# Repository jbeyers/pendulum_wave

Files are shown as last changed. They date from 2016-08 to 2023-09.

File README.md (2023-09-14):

# A perpetual pendulum wave machine

## What is it?

A pendulum wave is formed by a row of pendulums, each with a slightly different period. When started at the same time, they swing in a row, but quickly turn into a sinewavey snake shape, go through a whole set of interesting patterns and then end up in a straight row again.

The only ones I've seen are started and tuned manually.

## But perpetual?

Using steel bearing balls with magnets for the pendulums, and giving them a bit of a kick every now and again with a wire solenoid coil, the pendulums can be made to swing continuously. However, they would go out of tune after a few cycles.

The length of the pendulums are adjustable, so I can get them pretty close.

Getting the pendulums to vary their period is the tricky bit. This is slightly difficult to explain, but since the pendulums are built with fishing line, I can add a secondary pivot point below the first one, which will only kick in once the swing is larger than a certain angle. This causes the overall period to shorten if the angle increases.

Each coil has a sensing circuit to detect the pendulum swinging overhead. The coil is slightly offset to one side so that it can determine the direction of the swing from the slight difference in sensing time between the left and right swings.

Each coil is pulsed under PID control, so they sync up no matter what the initial positions are.

## License

This repository contains various files. In general, licensing is CC-BY-SA-4.0 for the designs and MIT for the software. Let me know if you need clarification.

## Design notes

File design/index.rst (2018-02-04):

Basic design
============

The design uses a frame made from square aluminium tubing, with 3D printed corner brackets I designed because I did not like any of the ones I found on Thingiverse. See `here<https://www.thingiverse.com/thing:2781519>`_ for the thingiverse design and the parts folder for the code.

Using a square box design is not the most stiff option, but it does allow me to resize the whole thing as I see fit.

The square tubing cut list spreadsheet has the list of cut lengths. I also designed brackets at the top to hang and adjust each pendulum to easily get the correct length for the period of the pendulum. The clips for the bearing balls are 3D printed and then drilled to ensure a smooth path for the line to go through. They simply clip onto the balls.

For the electromagnets, I got some 0.2mm wire from a friend. Doing 750 turns of wire around an air core should give me enough of an electromagnet to give the bearing balls a kick in the right direction. The coil will be slightly offset from each ball, to ensure that we can sense the direction.  

Sources:
--------

- Mantech: http://www.mantech.co.za/ProductInfo.aspx?Item=352M0029
- Banggood: https://www.banggood.com/0_2mm100m-Red-Copper-Magnet-Wire-Welding-Cable-Enameled-Wire-p-1081668.html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
- Aliexpress example: https://www.aliexpress.com/item/500-m-Free-shipping-0-19-mm-red-new-polyurethane-enameled-copper-wire-QA-1-130/2053713657.html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,searchweb201602_5_10152_10065_10151_10068_10344_10342_10343_10340_10341_10307_10060_10155_10154_10056_10055_10054_5370015_10059_10534_10533_10532_100031_10099_10338_10339_5580015_10103_10102_10052_10053_10142_10107_10050_10051_10174_10084_10083_10080_10082_10081_10110_5590015_10111_10112_10113_10114_143_10312_10314_10078_10079_10073-10051_10152_10111,searchweb201603_17,ppcSwitch_2&btsid=18ab4963-68ff-4cec-b533-50de82513f60&algo_expid=407fab98-5dce-4f39-aad7-5f68ff6fdf36-8&algo_pvid=407fab98-5dce-4f39-aad7-5f68ff6fdf36
- Ebay: http://www.ebay.com/itm/WINDING-WIRE-Copper-Enamelled-400g-Spool-0-10mm-3-00mm-/201975127992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

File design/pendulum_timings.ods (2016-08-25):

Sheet: Sheet1
Millisecond timings for 12 pendulums
Pendulum | 1 | 2 | 3 | 4 | 5 | 6 | 7 | 8 | 9 | 10 | 11 | 12
swings in 60 seconds | 64 | 63 | 62 | 61 | 60 | 59 | 58 | 57 | 56 | 55 | 54 | 53
period (ms) | 937.5 | 952.380952381 | 967.7419354839 | 983.6065573771 | 1000 | 1016.9491525424 | 1034.4827586207 | 1052.6315789474 | 1071.4285714286 | 1090.9090909091 | 1111.1111111111 | 1132.0754716981
integer ms period | 937 | 952 | 967 | 983 | 1000 | 1016 | 1034 | 1052 | 1071 | 1090 | 1111 | 1132
Last period error using integers | 32 | 24 | 46 | 37 | 0 | 56 | 28 | 36 | 24 | 50 | 6 | 4
Pendulum length (mm) | 218.3250114769 | 225.3109717837 | 232.637681324 | 240.3276664901 | 248.4053463915 | 256.897226949 | 265.8321186116 | 275.2413810433 | 285.1591986638 | 295.6228915734 | 306.67326715 | 318.3550185153
String length | 586.6500229539 | 600.6219435674 | 615.275362648 | 630.6553329801 | 646.8106927831 | 663.794453898 | 681.6642372233 | 700.4827620865 | 720.3183973275 | 741.2457831468 | 763.3465343001 | 786.7100370306
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

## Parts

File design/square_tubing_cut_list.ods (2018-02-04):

Pendulum wave box structure, lengths of 20mm aluminium square tubing needed
Box outside height | 395
Box outside depth | 200
Box outside width | 710
Square tubing width | 20
kerf width | 2
Item | Amount | Length (mm) | total
w side | 4 | 670 | 2680
depth side | 4 | 160 | 640
uprights | 4 | 355 | 1420
Top center spar | 2 | 670 | 1340
kerfs | 14 | 2 | 28
Total |  |  | 6108

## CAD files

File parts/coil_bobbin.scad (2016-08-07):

a = 25.8; // Overall length
b = 0.4; // flange thickness
c = 10.0; // flange diameter
d = 6.8; // ID of bobbin
e = 0.42; // Wall thickness

$fs=0.02;
translate ([0,0,a/2]) {
    // Center pillar
    difference() {
        union() {
            difference() {
                cylinder(a, r=c/2, center=true);
                cylinder(a-b*2, r=c/2, center=true);
                }
            cylinder(a, r=d/2 + e, center=true);
        }
        cylinder(a, r=d/2, center=true);
    }
}

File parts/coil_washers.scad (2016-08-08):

a = 0.8; // washer thickness
b = 3.2; // washer rim width
c = 6.4; // washer ID

$fs=0.02;
translate ([0,0,a/2]) {
    difference() {
        cylinder(a, r=(b+c)/2, center=true);
        cylinder(a, r=c/2, center=true);
    }
}

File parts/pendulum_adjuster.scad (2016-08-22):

a = 6; // Gap between bars
b = 20; // width of the bars
c = 29; // Width of whole thing
e = 3; // Outside wall thickness, and 45 degree area width
f = 160; // length of bar this must be in center of
g = 4; // Slot width for cable tie
h = 20; // Slide length
i = 4.5; // Screw hole diameter
j = 6.8; // Nut width
k = 0.5; // Slot for line
d = c-e-e; // Width of slot
m = 300; // Long distance for cutouts
n = 1; // Extra bit so cutouts go through without rendering
o = 1.6; // Thickness of cylinder springs for slider

t = 0.25; // tolerance

bar = [b+t+t, c, b+t];
l = e+t+b+t+f/2-(a/2+t+b+t+e);

$fs=0.02;

//pivot();
//translate([0, 35, 0]) adjuster();
//translate([0, 70, 0]) anchor();
translate([0, 105, 0]) slider();
//translate([0, 0, 0]) bar_support();


module pivot () {
    difference() {
        // Main block
        cube([e+t+b+t+a+t+b+t+e, c, b/2+e]);
        // Slots for bars to fit in
        translate([e, 0, e]) cube(bar);
        translate([e+t+b+t+a, 0, e]) cube(bar);
        // Cutout for free-hanging line
        translate([e+t+b+t, (c-d)/2, e]) cube([a, d, b]);
        // slot for line to go through
        translate([e+t+b+t, (c-d)/2, 0]) cube([a/2, d, b]);
        translate([e+t+b+t+a/2, (c-d)/2, e]) rotate([0,135,0]) cube([b, e, b+t+e]);
        translate([e+t+b+t+a/2, (c-d)/2+d-e, e]) rotate([0,135,0]) cube([b, e, b+t+e]);
        // Cable tie slot
        translate([0,(c-g)/2,-n]) cube([g/2, g, m]);
        // Slot to fit adjustment strip
        translate([e+t+b+t+a+t+b+t+e,c/2,0]) {
            translate([-e,-1.5*e-t,-n]) cube([e,t+3*e+t,m]);
            translate([-e-t-e-t,-2.5*e-t,-n]) cube([t+e+t,t+5*e+t,m]);
        }
    }
}


module adjuster () {
    difference() {
        // Main shape
        union() {
            cube([e,c,b/2+e]);
            translate([0,e,0]) cube([l, c-2*e, e]);
            // Slot to fit adjustment strip
            translate([l,c/2,0]) {
                translate([0,-1.5*e+t,0]) cube([t+e+t,3*e-2*t,e]);
                translate([t+e+t,-2.5*e+t,0]) cube([e-2*t,5*e-2*t,e]);
            }
        }
        translate([l,c/2-g/2,0]) cube([e, g, m]);
        // slot for cable tie
        translate([0,(c-g)/2,0]) cube([g/2, g, b+t+e]);
        // Slot for screw adjuster
        translate([e+t+b,c/2,0]) {
            translate([0,-c/4-t,0]) cube([t+e+t,t+c/2+t,e]);
            translate([t+e+t,-g/2,0]) cube([g,g,e]);
        }
    }
}


module anchor () {
    difference() {
        // Main shape
        hull() {
            translate([0,e+t,0]) cube([e,c-2*e-2*t,e]);
            translate([b+10,c/2,0]) cylinder(e, r=c/2-e-t);
        }
        // Slot and hole for cable tie
        translate([0,(c-g)/2,e-g/2]) cube([b+e,g,g]);
        translate([b+e,(c-g)/2,0]) cube([g/2,g,e]);

        translate([b+10,c/2,e]) cylinder(b,r=i/2,center=true);
        cube([b+e,c/4+t,e]);
        translate([0,3*c/4-t,0]) cube([b+e,c/4+t,e]);
    }
}

module slider() {
    difference() {
        // Main shape
        union() {
            translate([e,0,0]) cube([2*e,c,b]);
            translate([e,c/5,0]) cylinder(b,r=c/5,center=false);
            translate([e,4*c/5,0]) cylinder(b,r=c/5,center=false);
            translate([2*e,0,0]) cube([b,c,2*e]);
            // Slot to fit adjustment strip
        }
        // Hollow out the cylinders
        translate([e,c/5,0]) cylinder(b,r=c/5-o,center=false);
        translate([e,4*c/5,0]) cylinder(b,r=c/5-o,center=false);
        // slot for slider
        translate([e+0.4,e-2*t,0]) cube([t+e+t-0.4,c-2*e+4*t,b]);

        // Bolt and nut capture
        translate([3*e,(c-j)/2-t,e]) cube([b,j+2*t,2*e]);
        translate([e+10,c/2,e]) cylinder(b,r=i/2,center=true);
        // Line guides
        translate([e+10,0,e]) cylinder(b,r=i/2,center=true);
        translate([e+10,c,e]) cylinder(b,r=i/2,center=true);
        // Line capture slot
        translate([2*e+10+5,(c-k-t)/2,0]) cube([b,k+2*t,b]);
    }
}


module bar_support () {
    support_l = 2*b+4*t+a+2*e;
    difference() {
        // Main block
        cube([e+2*t+b+c,support_l, b/2+e]);
        // Bar cutouts
        translate([e,0,e]) cube([b+2*t,m,b]);
        translate([e,e,e]) cube([m,b+2*t,b]);
        translate([e,e+b+2*t+a,e]) cube([m,b+2*t,b]);
        translate([2*e+2*t+b,e+b+2*t+a/2,0]) {
            translate([0,-b/2-t,0]) cube([m,b+2*t,b]);
            translate([-g/2,-g/2,0]) cube([g,g,b]);
        }
        // Cable tie slots
        translate([-g/2,support_l/2-g/2,0]) cube([g,g,b]);
        translate([e+2*t+b+c/2-g/2,-g/2,0]) cube([g,g,b]);
        translate([e+2*t+b+c/2-g/2,support_l-g/2,0]) cube([g,g,b]);
    }
}

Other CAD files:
parts/pendulum_adjuster_anchor.scad
parts/corner_bracket.scad
parts/pendulum_adjuster_slide.scad
parts/pendulum_ball_holder.scad
parts/pendulum_pivot.scad

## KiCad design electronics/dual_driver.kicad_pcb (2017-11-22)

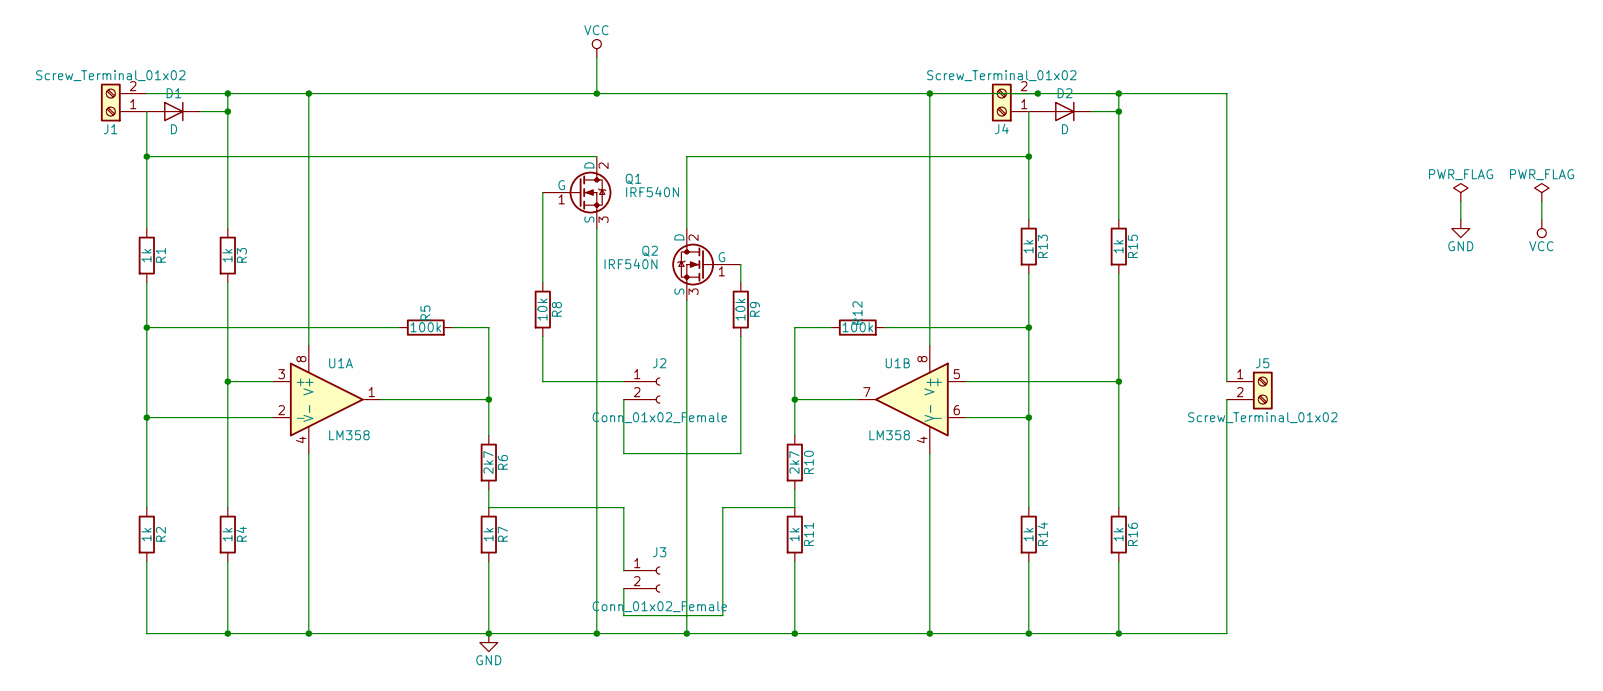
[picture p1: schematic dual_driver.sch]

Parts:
D1, D2: D; D_DO-41_SOD81_P2.54mm_Vertical_AnodeUp
J1, J4: Screw_Terminal_01x02; TerminalBlock_Phoenix_MPT-2.54mm_2pol
J2, J3: Conn_01x02_Female; Socket_Strip_Straight_1x02_Pitch2.54mm
J5: Screw_Terminal_01x02; TerminalBlock_bornier-2_P5.08mm
Q1, Q2: IRF540N; TO-220-3_Vertical
R1, R2, R3, R4, R7, R11, R13, R14, R15, R16: 1k; R_Axial_DIN0516_L15.5mm_D5.0mm_P20.32mm_Horizontal
R5, R12: 100k; R_Axial_DIN0516_L15.5mm_D5.0mm_P20.32mm_Horizontal
R6, R10: 2k7; R_Axial_DIN0516_L15.5mm_D5.0mm_P20.32mm_Horizontal
R8, R9: 10k; R_Axial_DIN0516_L15.5mm_D5.0mm_P20.32mm_Horizontal
U1: LM358; DIP-8_W7.62mm

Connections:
GND: J5.2, Q1.3 (S), Q2.3 (S), R2.2, R4.2, R7.2, R11.2, R14.2, R16.2, U1.4 (V-)
unnamed: D1.2 (A), J1.1, Q1.2 (D), R1.1
unnamed: D2.2 (A), J4.1
unnamed: J2.1, R8.2
unnamed: J2.2, R9.2
unnamed: J3.1, R6.2, R7.1
unnamed: J3.2, R10.2, R11.1
unnamed: Q1.1 (G), R8.1
unnamed: Q2.1 (G), R9.1
unnamed: Q2.2 (D), R13.1
unnamed: R1.2, R2.1, R5.1, U1.2 (-)
unnamed: R3.2, R4.1, U1.3 (+)
unnamed: R5.2, R6.1, U1.1
unnamed: R10.1, R12.1, U1.7
unnamed: R12.2, R13.2, R14.1, U1.6 (-)
unnamed: R15.2, R16.1, U1.5 (+)
VCC: D1.1 (K), D2.1 (K), J1.2, J4.2, J5.1, R3.1, R15.1, U1.8 (V+)

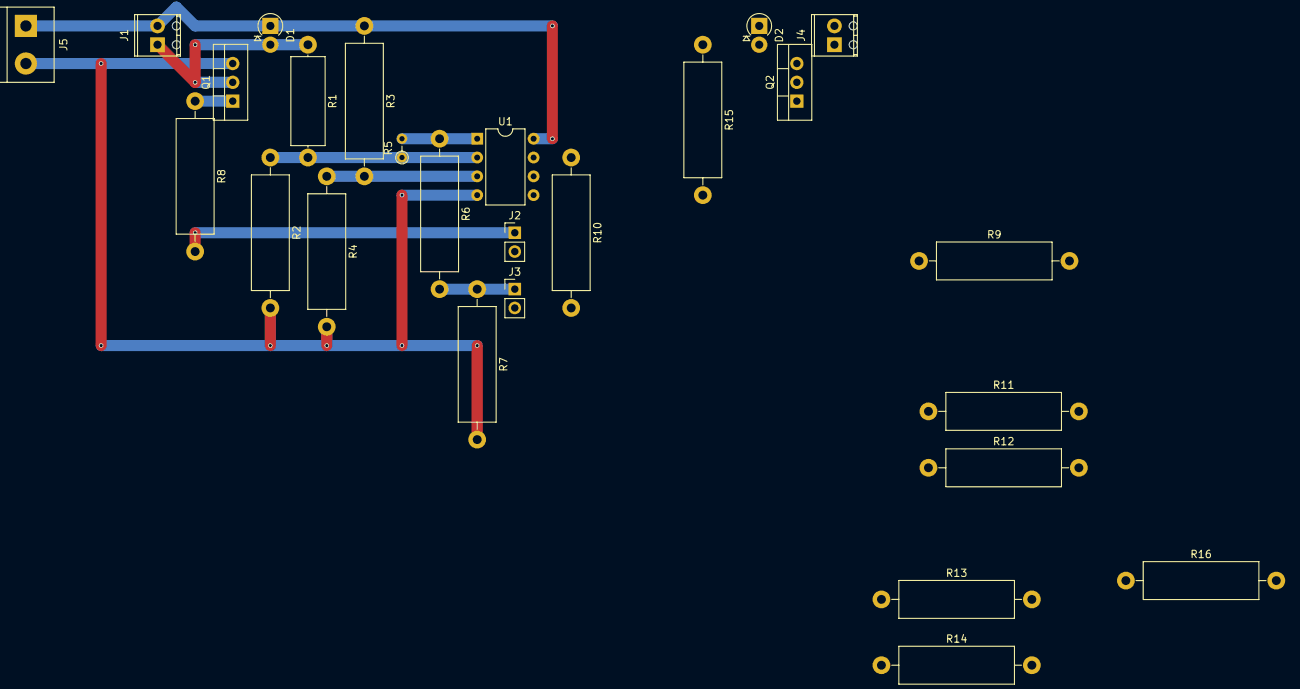
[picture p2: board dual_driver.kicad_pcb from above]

Board: 2 copper layers, 26 parts (0 on the bottom side), 17 nets.

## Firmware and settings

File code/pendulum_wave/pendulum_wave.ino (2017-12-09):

const int trigger_level = 128; // deviation from average needed for the sensor to trigger.
const float first_tempo = 61.0; // Tempo in bpm of the first pendulum
const unsigned long pulse = 40ul; // Driver pulse length in milliseconds.
const unsigned long lockout = 350ul; // Sensor lockout after triggered, in milliseconds.
const unsigned long switch_lockout = 1400ul; // Sensor lockout after triggered, in milliseconds.
const int pendulums = 8;

unsigned long now; // The millis count for the current main loop
int sensors[pendulums]; // The immediate sensor readings
int averages[pendulums]; // Sensor long-term averages
unsigned long lockouts[pendulums]; // Trackers for the lockout timings
unsigned long pulses[pendulums]; // Trackers for the pulses
float ideal_periods[pendulums]; // Swing period for each pendulum. Needed to accurately control speed.
float wheres[pendulums]; // Swing period for each pendulum. Needed to accurately control speed.
float integrals[pendulums]; // Swing period for each pendulum. Needed to accurately control speed.
float derivatives[pendulums]; // Swing period for each pendulum. Needed to accurately control speed.
float proportionals[pendulums]; // Swing period for each pendulum. Needed to accurately control speed.
unsigned long average_periods[pendulums]; // Keep the previous swing trigger timestamps for imbalance calculations.
unsigned long expected_triggers[pendulums]; // When we expect the next positive trigger.
unsigned long previous_triggers[pendulums]; // Keep the previous swing trigger timestamps for imbalance calculations.
unsigned long previous_triggers_2[pendulums]; // Keep the previous swing trigger timestamps for imbalance calculations.
unsigned long pulse_widths[pendulums]; // Keep the previous swing trigger timestamps for imbalance calculations.
int trigger_counts[pendulums]; // Count positive triggers to implement a state machine
bool should_pulse[pendulums];
int imbalances[pendulums]; // Track imbalance in the swing length.
bool pos[pendulums]; // flag if this is a positive or negative swing direction. positive is the one taking longer.
float where; // Computes where in the cycle we are.
float modulo; // computes where in the swing we are.
int i; // Loop iterator
int j; // Loop iterator
int pendulum_to_view = -1; //Which pendulum to view
unsigned long switch_time;
unsigned long pulse_width;
int min_counts;
int display_function;
// PID loop parameters;
float loop_p;
float loop_i;
float loop_d;
float p_value;
float d_value;

void setup() {
  Serial.begin(9600);
  // initialize serial communications at 9600 bps:
  now = millis();
  switch_time = now;
  display_function = 0;
  loop_p = 1.0;
  loop_i = 1.0/32.0; // Small, so it takes a while to settle, but does not go haywire.
  loop_d = 10.0;
  p_value = 0.0;
  d_value = 0.0;
  for ( i = 0; i < pendulums; i++ ) {

    // Lock out the counters and timers for 10 seconds, enough for the averages to settle
    lockouts[i] = now + 10000ul;

    // Set the period for each pendulum
    ideal_periods[i] = 60000.0 / (first_tempo - (float)i);

    // Initial values for average periods
    average_periods[i] = 60000ul / (long(first_tempo) - long(i));

    // Trigger counts
    trigger_counts[i] = 0;

    // Set the output pins
    pinMode(i + 2, OUTPUT);
  }
}

// The main loop is assumed to take 2-3 ms to run. 1 for analog reads, 1 for
// delay, 1 for the main code loop.
void loop() {
  now = millis();
  if (Serial.available() > 0 ) {
    display_function = Serial.parseInt();
    Serial.print("Switching to function ");
    Serial.print(display_function);
    Serial.println();
  }

  if ( now - switch_time > 2001 ) {
    switch_time = now;
    pendulum_to_view += 1;
    if (pendulum_to_view > 7) {
      pendulum_to_view = 0;
    }
    if (display_function == 0) {
      Serial.print(pendulum_to_view);
      Serial.print(" | where = ");
      Serial.print(where);
      Serial.print(" | imb= ");
      Serial.print(imbalances[pendulum_to_view]);
      Serial.print(" | ideal = ");
      Serial.print(ideal_periods[pendulum_to_view]);
      Serial.print(" | actual = ");
      Serial.print(average_periods[pendulum_to_view]);
      Serial.println();
    } else if (display_function == 1) {
      Serial.print("where");
      for ( j = 0; j < pendulums; j++ ) {
        Serial.print(" | ");
        Serial.print(wheres[j]);
      }
      Serial.println();
    } else if (display_function == 2) {
      Serial.print("imbalances");
      for ( j = 0; j < pendulums; j++ ) {
        Serial.print(" | ");
        Serial.print(imbalances[j]);
      }
      Serial.println();
    } else if (display_function == 3) {
      Serial.print("periods");
      for ( j = 0; j < pendulums; j++ ) {
        Serial.print(" | ");
        Serial.print(ideal_periods[j]);
        Serial.print("/");
        Serial.print(average_periods[j]);
      }
      Serial.println();
    } else if (display_function == 4) {
      Serial.print("pids");
      for ( j = 0; j < pendulums; j++ ) {
        Serial.print(" | ");
        Serial.print(proportionals[j]);
        Serial.print("/");
        Serial.print(integrals[j]);
        Serial.print("/");
        Serial.print(derivatives[j]);
      }
      Serial.println();
    } else if (display_function == 5) {
      Serial.print("pulses");
      for ( j = 0; j < pendulums; j++ ) {
        Serial.print(" | ");
        Serial.print(pulse_widths[j]);
      }
      Serial.println();
    }
  }

  for ( i = 0; i < pendulums; i++ ) {

    // Read the sensor
    sensors[i] = 16 * analogRead(i);

    // average holds a slow-moving long-term average of the sensor reading. The
    // way we compute it should result in insensitivity to spikes.
    // Note: The multiplication factor above allows us to do integer math here.
    // The sensor value is 0-1023, so the average will never be more than 17000.
    if ( sensors[i] > averages[i]) {
      averages[i] = averages[i] + 1;
    }
    if ( sensors[i] < averages[i]) {
      averages[i] = averages[i] - 1;
    }

    // Trigger detection of a magnet entering
    if ((sensors[i] > (averages[i] + trigger_level)) && (lockouts[i] < now )) {

      // Reset the lockout. This prevents spurious triggering which could throw off the position
      lockouts[i] = now + long(ideal_periods[i] * 0.4);

      // Change swing direction.
      pos[i] = !pos[i];

      // The triggers trigger every time the magnet passes the coil. We only want to work on the positive swing.
      if (pos[i]) {

        // Over time we see if the current swing is longer than the previous
        // one. The coil that senses the swing is off-center, so over time we
        // expect the tally to go up (if our assumption of swing direction is
        // correct) or down (if it's not).  Tally the swing imbalance and if
        // it's the reverse of what we expect, reverse the swing directions.
        // Four gives us a nice balance here: It's slow enough that spurious
        // signals will not shift it, and it's fast enough that if it does, it
        // will switch back before the pendulum gets totally out of sync.
        if (now - previous_triggers[i] >= previous_triggers[i] - previous_triggers_2[i]) {
          if (imbalances[i] < 4) {
            imbalances[i]++;
          }
        } else {
          imbalances[i]--;
          if (imbalances[i] < -4) {
            imbalances[i] = 4;
            pos[i] = !pos[i];
          }
        }

        // Where in the cycle should we be?
        where = (now % 60000ul)/ideal_periods[i];
        wheres[i] = where - 0.25;
        modulo = where - (int)where;

        // These numbers are needed for the PID control loop. We need to know:
        // * How far behind we are (proportional)
        // * How fast we are catching up (derivative)
        // * How much we should offset the value for (integral)

        // The modulo is always positive. Shift it by a quarter, so that we can
        // do calculations around the zero point. We need this because the
        // modulo is circular: If more than 0.75, it is considered to be fast
        // for the next cycle, instead of slow for this one. 0.75 is chosen
        // because we can actively control the cycle from 0.75 down to 0, while
        // if it's bigger, we need to just not power anything and hope that it
        // will slow down enough without losing the count.
        modulo = modulo - 0.25;

        // proportional
        p_value = min(modulo * ideal_periods[i] * loop_p, 40);
        proportionals[i] = p_value;

        // integral calculations.
        // This is not really an integral calculation, just a long-running
        // moving average. Same result, but both faster-settling and slower to
        // go haywire, I think.
        if ( modulo < 0.0 && integrals[i] >= -40.0) {
          integrals[i] = integrals[i] - loop_i;
        } else if ( modulo > 0.0 && integrals[i] <= 40.0) {
          integrals[i] = integrals[i] + loop_i;
        }

        // Derivative is the period compared to the ideal one.
        d_value = (ideal_periods[i] - (float)average_periods[i]) * loop_d;
        derivatives[i] = d_value;

        // Work out the pulse width
        pulse_width = long(min(max(p_value + integrals[i] - d_value, 0.0), 40.0));
        pulse_widths[i] = pulse_width;

        // Update the trigger counts
        trigger_counts[i] = trigger_counts[i] + 1;

        // Update the expected next pulse start and stop times only if we are not actively triggering
        if (trigger_counts[i] > 2) {
          expected_triggers[i] = now + average_periods[i];
          if (pulse_width > 0) {
            pulses[i] = expected_triggers[i] + pulse_width;
          }
        }
        // Update the average periods
        if (now - previous_triggers_2[i] < average_periods[i]) {
          average_periods[i] -= 1ul;
        } else if (now - previous_triggers_2[i] > average_periods[i]) {
          average_periods[i] += 1ul;
        }
      }

      // Update the previous trigger times
      previous_triggers_2[i] = previous_triggers[i];
      previous_triggers[i] = now;

    }

    min_counts = 10;
    for ( j = 0; j < pendulums; j++ ) {
      min_counts = min(trigger_counts[j], min_counts);
    }
    if (min_counts > 2) {
      for ( j = 0; j < pendulums; j++ ) {
        trigger_counts[j] = 0;
      }
    }

    // Write out the pulse
    if ( now < pulses[i] && now >= expected_triggers[i] && trigger_counts[i] < 2) {
      digitalWrite(i + 2, HIGH);
    } else {
      digitalWrite(i + 2, LOW);
    }
  }

  // wait for the analog-to-digital converter to settle after the last reading
  //delay(1);

}

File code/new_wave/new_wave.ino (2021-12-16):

#include <Servo.h> 

// Create the servo objects
Servo servox;

int low_pos;
int high_pos;
unsigned long period;
unsigned long low_time;
unsigned long current;
unsigned long new_millis;

void setup() { 
  servox.attach(9);  // Attach the servo
  current = millis();
  period = 1022;
  low_time = period*500/1000;
  low_pos = 90;
  // high_pos = 93;
  high_pos = 145;
  pinMode(13, INPUT_PULLUP);
} 

void loop() { 
  if (millis() > current + period) {
    current = current + period;
    servox.write(low_pos);
  } else if ((millis() > current + low_time) && digitalRead(13)) {
    servox.write(high_pos);
  }
}

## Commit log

2016-07-23 Holder for the pendulum balls added
    [pendulum_ball_holder.scad, pendulum_ball_holder.stl]
2016-07-25 Add square tubing cut list spreadsheet
    [square_tubing_cut_list.ods]
2016-07-27 Calculate pendulum timings
    [pendulum_timings.ods]
2016-08-07 Remove stl files
    [pendulum_ball_holder.stl]
2016-08-07 Added extra cross items
    [square_tubing_cut_list.ods]
2016-08-07 Some parts added
    [coil_bobbin.scad, corner_bracket.scad, pendulum_adjuster.scad]
2016-08-07 Simple washers
    [coil_washers.scad]
2016-08-08 Thicker washers
    [coil_washers.scad]
2016-08-09 Basic adjuster
    [pendulum_adjuster.scad]
2016-08-16 Parts all created individually
    [corner_bracket.scad, pendulum_adjuster.scad, pendulum_adjuster_anchor.scad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]
2016-08-16 Combine fitting parts into assembly
    [pendulum_adjuster.scad]
2016-08-22 Tweak parts
    [pendulum_adjuster.scad]
2016-08-23 Line length calc for pendulums
    [pendulum_timings.ods]
2016-08-25 Newer attempt at setting timings
    [pendulum_timings.ods]
2017-10-03 Add notes after ordering magnet wire
2017-11-22 Add pcb design files
    [dual_driver.kicad_pcb, dual_driver.sch]
2017-11-22 Ignore kicad pcb and autogenerated files
2017-12-01 Semi-working, but switching too slowly
    [pendulum_wave.ino]
2017-12-02 Switch randomly and proportional control
2017-12-02 Clamp proportional and remove trigger levels
2017-12-02 Cleanup and fix logic
    [pendulum_wave.ino]
2017-12-03 Faster imbalance correction, better diagnostics. It Works!
    [pendulum_wave.ino]
2017-12-08 Lots of comments, little bit of code. Prep for PID
2017-12-09 PID control
2018-02-04 Nice descriptions for thingiverse customizer
    [corner_bracket.scad]
2018-02-04 Adjust cut list with new dimensions
    [square_tubing_cut_list.ods]
2018-03-22 Added trimpots to schematic
    [dual_driver.sch]
2018-04-28 More solid ball holder with cutout for magnet
    [pendulum_ball_holder.scad]
2018-05-03 Larger magnet
    [pendulum_ball_holder.scad]
2018-05-04 Thicker holder
    [pendulum_ball_holder.scad]
2019-04-25 Minimum angle set for ball holders
    [pendulum_ball_holder.scad]
